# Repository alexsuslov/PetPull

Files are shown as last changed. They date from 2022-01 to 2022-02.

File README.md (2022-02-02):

# PetPull - станок для производства филамента из ПЭТ бутылок

Так что во избежание вселенского бурления - будем использовать название PetPull.
Во первых это название уже стало именем нарицательным. Первым был все же Моторист, а до него еще кто то.
Первые станки были не для для 3D печати, а для метелок...  

На основе разработок 

- Виталия Богачева

_кидайте issue если нужно что то поправить/добавить_

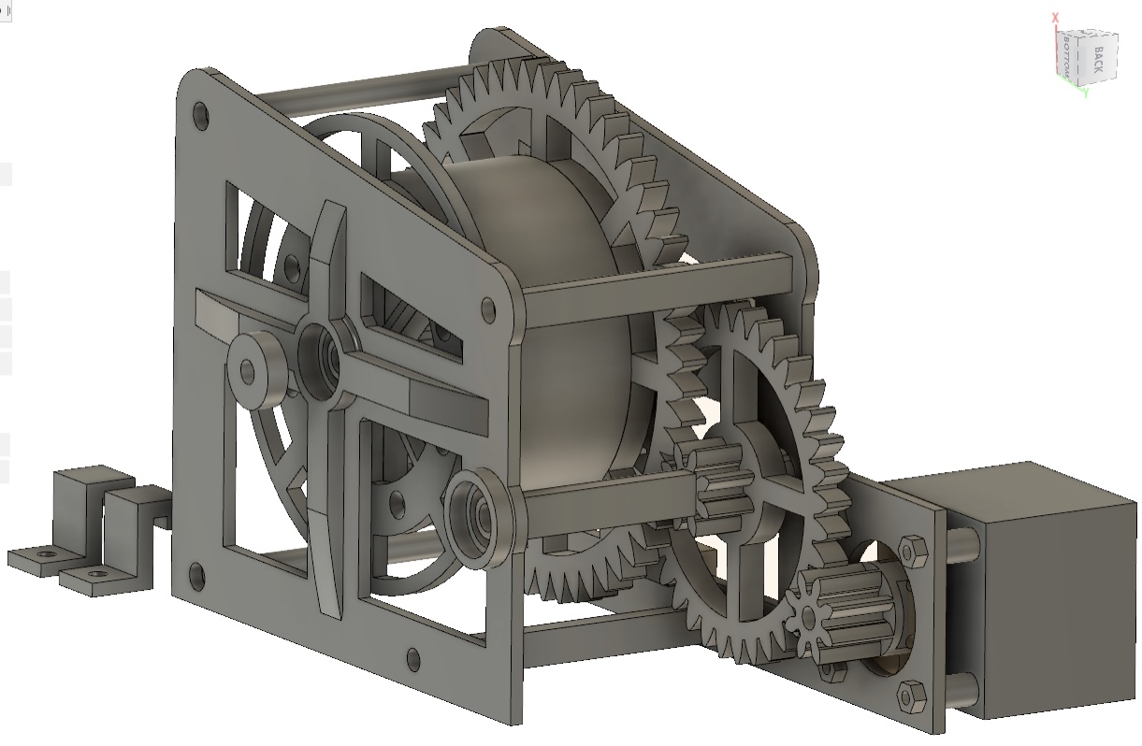
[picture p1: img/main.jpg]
main view


Простое, функциональное устройство для переработки бутылок в филамента.  

- [Обзорное видео тут](https://youtu.be/G16bqoB8Z38)
- [Схема устройства](pdf/2019-11-28V1.2.pdf)
- [Печатная плата для ЛУТ](https://drive.google.com/open?id=1dySD1lTDA4rSZQcVADHj6VBQWqIWLeg4)

## Материалы

- Двигатель - Nema 17
- Контроллер - Arduino Nano V3 
- Драйвер - A4988
- Дисплей - LCD 1602 (HD44780)
- Термистор - 100К от 3D принтера
- Нагреватель - 12V*40ВТ от 3D принтера 
- Блок нагревателя -  E3D Volcano от 3D принтера
- Сопло - 0,8мм диаметром для принтера Anet A6
- Металлический уголок из строительного магазина 
- Подшипники - 625ZZ (опционально) 16mm - 5mm

Маленькие саморезы для сборки составной детали бобины  и большие для крепления станка к основанию. 

## Характеристики 

- Энергопотребление - менее 40Вт*ч
- Скорость производства филамента ~ 10-20 см/мин
- Диаметр прутка - 1,7мм^2
- Заполнение прутка ~ 60-80%
- Рабочая температура ~ 160

## Руководство по самостоятельной сборке

- [Копус станка](assembly.md)
- [Сопло экструдера](extruder.md)
- [Бобина для намотки филамента](spool.md)
- [Контроллер скорости протяжки и температуры](controller.md)

## Температура. 
Вопреки оригинальному видео Виталия - я выяснил что температура 250-260С избыточна для производства филамента. В помещении начинает нещадно вонять, как на промзоне Парнас в Питере. При 160 градусах протяжка проходит ровно точно так же, но пластик почти ничем не пахнет.  Работоспособность станка сохраняется и при снижении температуры до 140С, но диаметр прутка начинает плавать. Видимо это не совсем подходящий режим волочения.  
[WIKI: Свойства PET(Полиэтилентерефталат) ](https://ru.wikipedia.org/wiki/%D0%9F%D0%BE%D0%BB%D0%B8%D1%8D%D1%82%D0%B8%D0%BB%D0%B5%D0%BD%D1%82%D0%B5%D1%80%D0%B5%D1%84%D1%82%D0%B0%D0%BB%D0%B0%D1%82)

## Минусы технологии

### Пруток короткий.
Прутки из бутылок получаются относительно короткими - 8-20 метров. Для печати большинства небольших деталей этого достаточно, но все же удобнее когда перед началом печати у Вас хотя бы сотня гарантированных метров пластика на катушке. 
Проблему может решить сварочный аппарат для прутков и я позже его продемонстрирую. В контроллере станка для него все предусмотрено.    
Пруток прямой и жесткий 
Норовит размотаться с катушки. Решить можно либо фиксацией свободного хода катушки, либо свиванием прутка при производстве. Пока не думал над этим. 
### Не пруток, а трубка
Думаю если сообщество подключится к вопросу - сможем обеспечить более плотное прессование ленты в прутке. Тут нужно экспериментировать. 
### Толщина ленты разнится от бутылки к бутылке
А следовательно пруток имеет разное заполнение и нужно как-то нормировать скорость подачи пластика. Пока не думал над этим. но думаю решаемо.
### Медленная скорость печати. 
Похоже особенность всего PET пластика.

## Плюсы технологии

Помимо очевидных, тертых-перетертых хочется отметить еще несколько. 

### Отсутствие страха остаться без филамента. 
Это реально круто, когда тебя не особо беспокоит сколько метров у тебя осталось в катушке. Ты знаешь, что если нужно - через пару часов будет столько сколько нужно. 
 
### Пластик более термостойкий и прочный чем ABS и PLA
Экспериментов еще не ставил, но что подсказывает мне что детали можно будет использовать в широких пределах температур и агрессивных средах. Шестерни и втулки из этого пластика реально очень прочные и износостойкие.

### Печать без головной боли
Вчера нужно было печатать ABSом. Время было дорого и нужно было поскорее завершить распечатку деталей.  Поймал себя на мысли что привыкнув печатать PETом, возвращаться к ABS, было неприятно. Это и горячий стол, и деламинация, и платно в конце концов. 

## Спайка прутка
Одно из главных неудобств при печати пластиком из бутылок - маленькая длина - всего 8-10 метров. Печатать объемные детали не удобно - нужно постоянно контролировать печать и своевременно менять материал. Задача сварки отрезков прутка - успешно решена. Расскажу как. 

### Теория
ПЭТ пластик плавится при температуре выше 260 градусов. При медленном охлаждении - кристаллизуется приобретая белый цвет,  прочность и хрупкость. При быстром охлаждении остается прозрачным и гибким. Для печати подходит второе состояние, следовательно для получения хорошего шва - нужно его быстро охладить. Требуемая скорость охлаждения около 70 градусов в секунду.  

### Блок нагрева
Для нагрева прутка я изготовил блок нагревателя из отрезка алюминиевого радиатора. В нем нужно просверлить сквозное отверстие диаметром 6мм под ТЭН, сквозное отверстие диаметром 4мм для термотрубки и глухое отверстие диаметром 2мм под датчик температуры. Последнее нужно сделать подальше от ТЭНа и поближе к термотрубке. 

После сварки нужно быстро охладить шов. Для этого подойдет алюминиевый или медный радиатор. В нем нужно сделать сквозное отверстие диаметром 4,2-4,5мм. Вдоль отверстия на поверхность делается пропил шириной 2-2,5мм для установки и извлечения прутка. 

Сварка ABS или PLA пластика не отличается от сварки PET прутка за исключением того что для нее нужна температура ниже - 160-200 градусов.

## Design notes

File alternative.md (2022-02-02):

- https://github.com/mvbasov/PETCTL
- https://t.me/s/PETPullGroup

<!-- нагреватель -->
- https://github.com/mvbasov/PETCTL/tree/github/3D_models/HeatedBlock

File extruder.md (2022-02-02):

# Экструдер

## Сопло экструдера.

В моем случае было использовано сопло изготовленное из болта с диаметром резьбовой части - 5 мм.

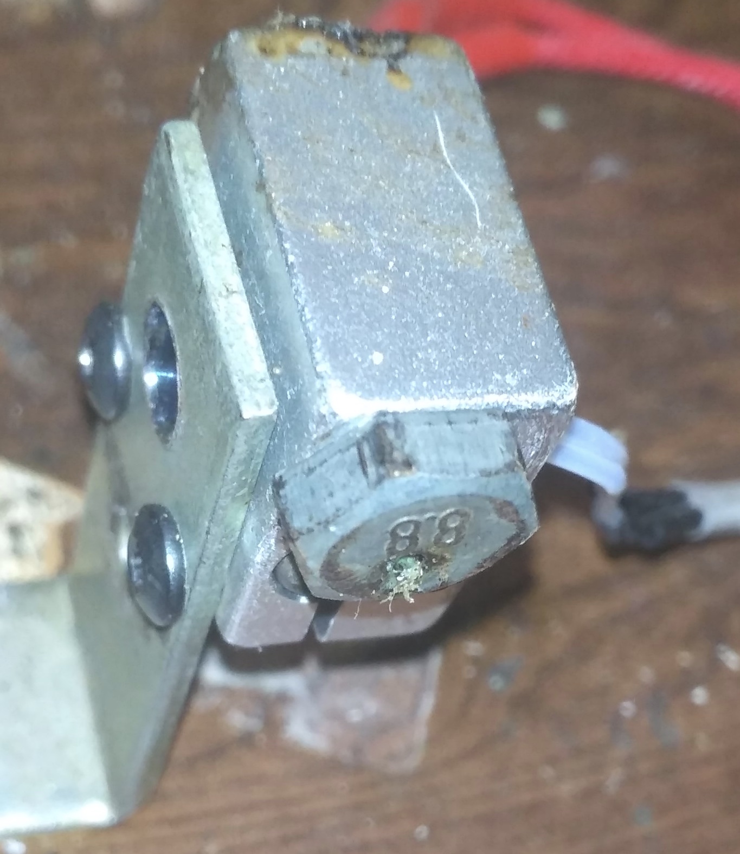
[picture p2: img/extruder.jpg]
extruder


Он был обрезан до общей длины ~10мм. Затем в центре было просверлено отверстие диаметром 2мм. Такой диаметр слишком большой для производства филамента, поэтому для его уменьшения был использован шарик от шарикоподшипника.  Несколько ударов молотка по шарику установленному на выходном отверстии экструдера - и его диаметр сужается до необходимых 1,7мм. 

У меня также был опыт использования в качестве экструдера штатных сопел устанавливаемых в принтер Anet A6. Но после нескольких неудачных попыток протяжки филамента - я отложил их до лучших времен. 
03,12,2019 - UPD 
Вполне неплохо показали себя рассверленые родные длииинные сопла для нагревателя вулкан.  
22,12,2019 - UPD

Сейчас делаю так. Беру болт М6 с длиной резьбовой части 10мм(накручиваем 2 гайки и отрезаем ножовкой). Затем подбираю сверло по фактическому диаметру 1,7мм и просверливаю болт насквозь. Затем раздаю перьевыми сверлами по кафелю. 

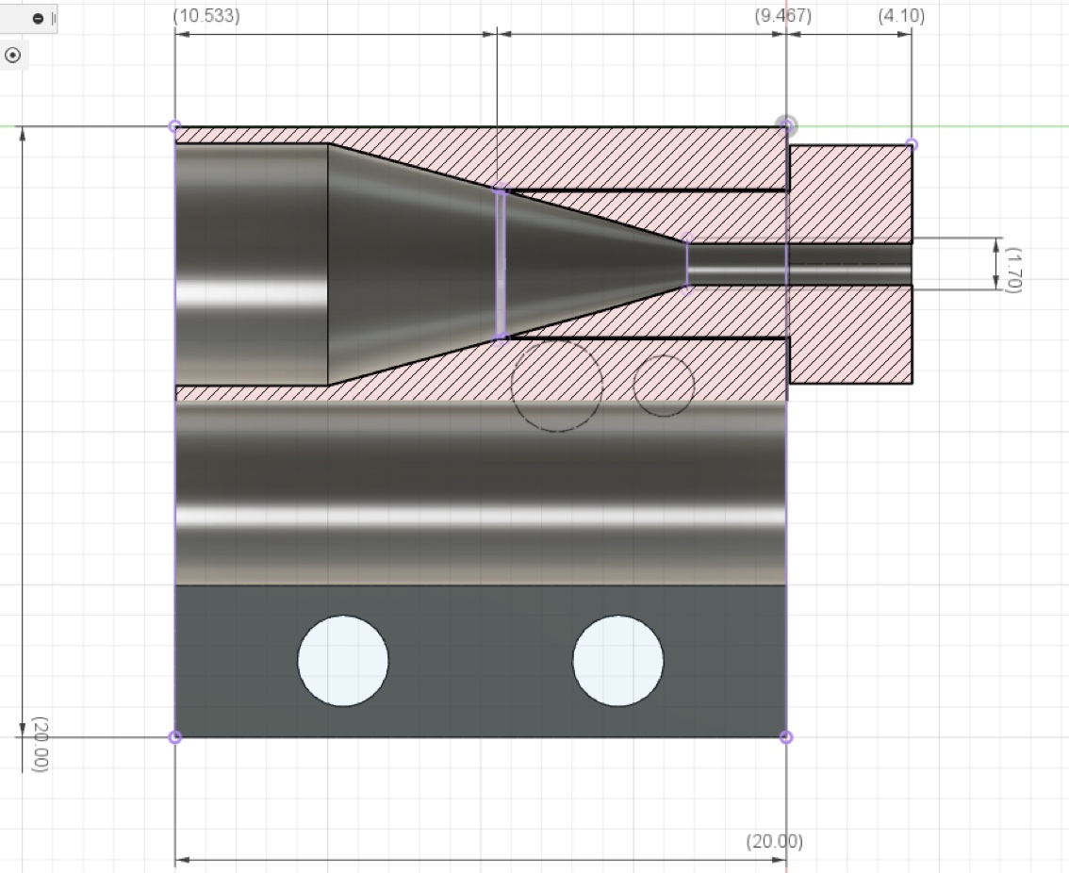
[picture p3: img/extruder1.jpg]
extruder1


## Нагреватель

Изготавливается путем высверливания конического отверстия в блоке Volcano

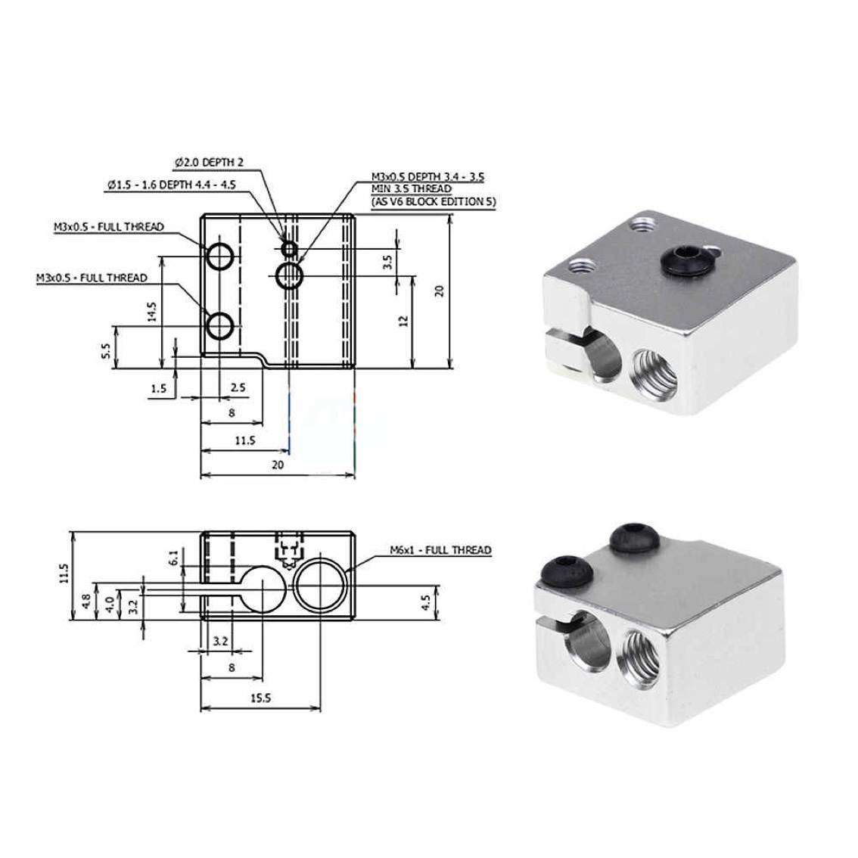
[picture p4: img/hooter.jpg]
hooter


с помощью перьевого сверла по кафелю, диаметром 8мм.

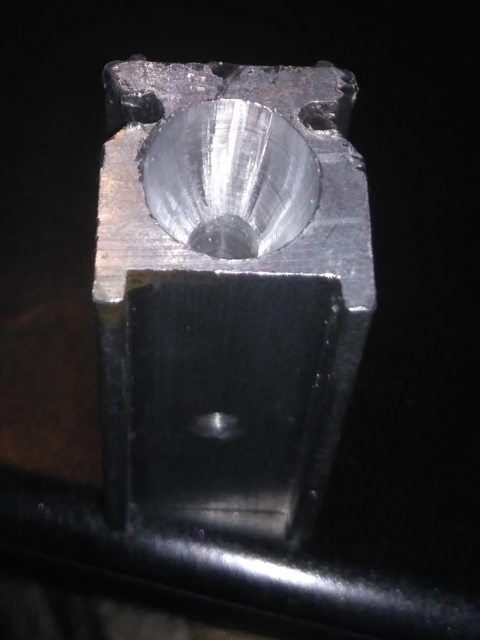
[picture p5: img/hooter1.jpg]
hooter1


Высверливание продолжается до тех пор пока кончик сверла не коснется латунной поверхности сопла. Контроль ведется визуально. 
Для крепления блока нагревателя к рабочему столу станка - используется обычный металлический строительный уголок. В нем просверливаются пару отверстий под штатные винты, зажимающие керамический ТЭН. 

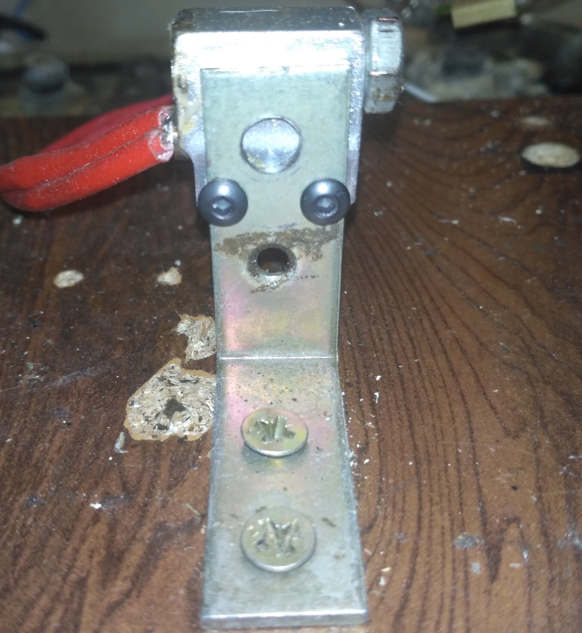
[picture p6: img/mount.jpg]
mount


Никакой теплоизоляции не используется. PID регулятор контроллера держит температуру в заданных пределах очень точно, компенсируя теплопотери. Ниже посекундный график, показывающий дрейф температуры в пределах нескольких разрядов АЦП на протяжении часа реальной работы станка. 

вот так выглядит общая работа ПИД регулятора. 

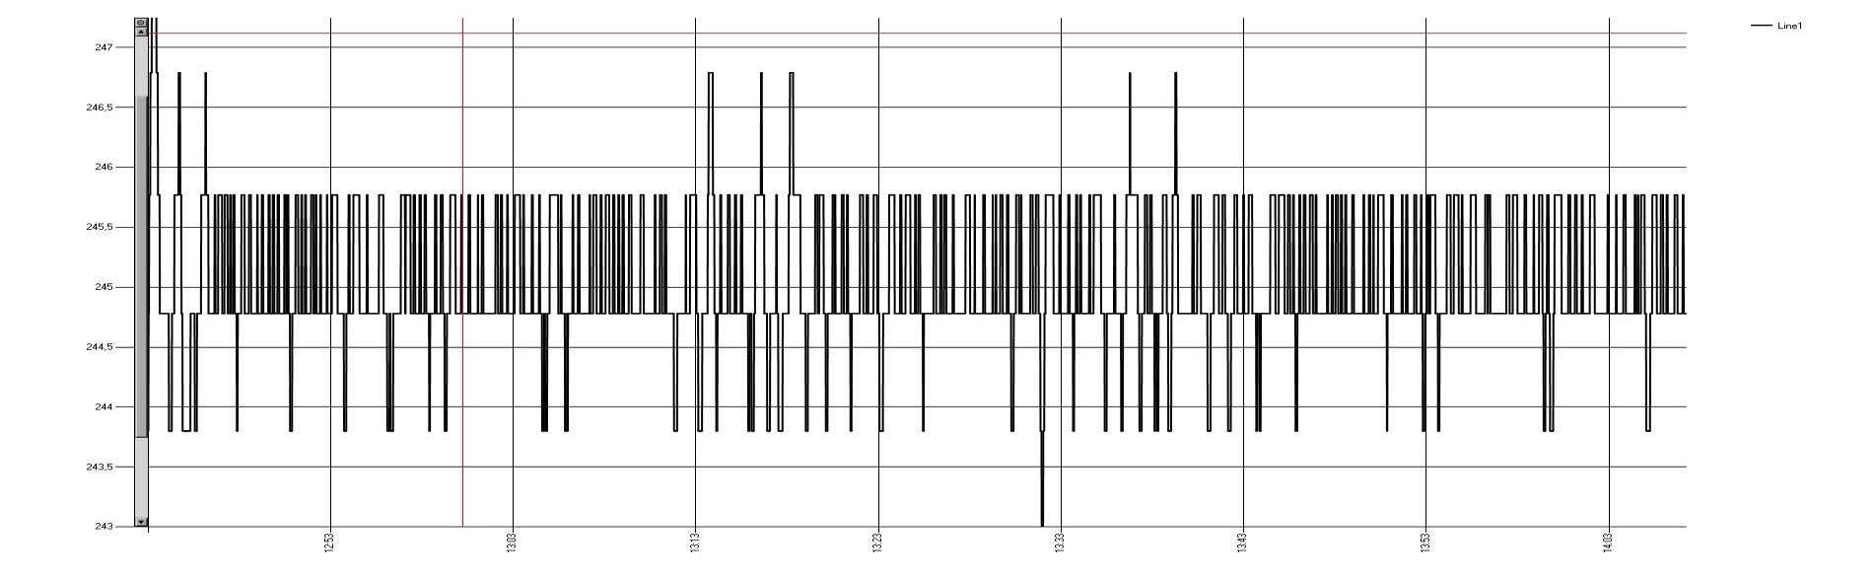
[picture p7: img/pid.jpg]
pid

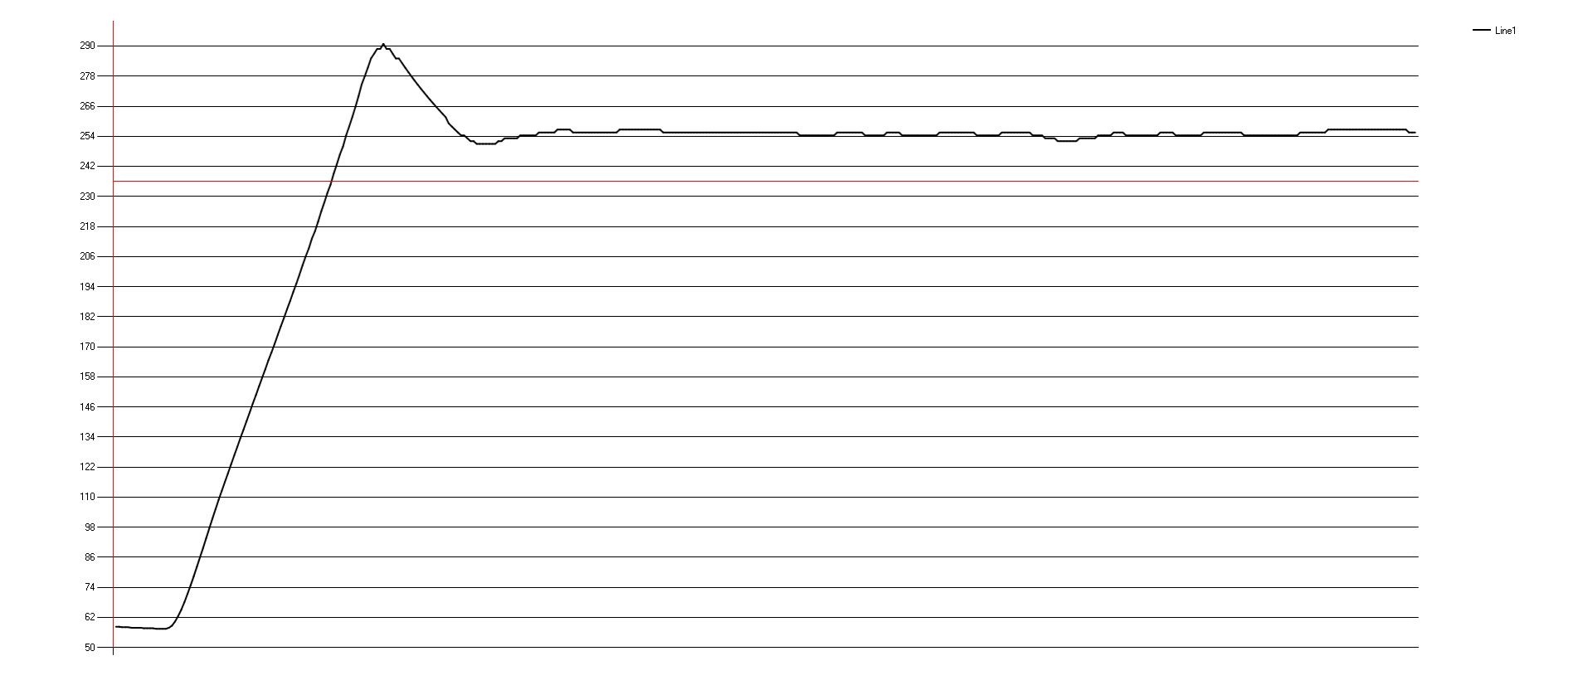
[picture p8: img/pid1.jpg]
pid1


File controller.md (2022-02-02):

# Контроллер скорости протяжки и температуры

Изготовлен на основе платки Arduino Nano V3.  Схема простейшая, не имеет дефицитных деталей, простая для повторения.  
Печатная плата выложена в репозитории. Хоть и полностью функциональная - пока не совсем готова для корпусирования. Опыта в этом у меня не много. Потому получается не с первого раза.

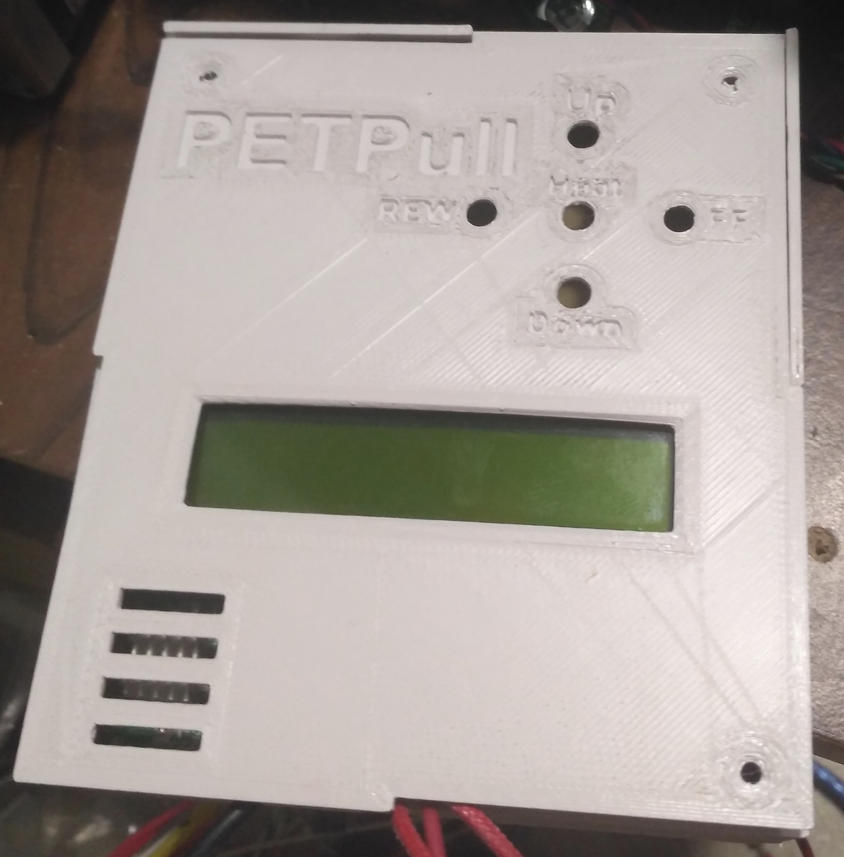
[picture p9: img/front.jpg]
front

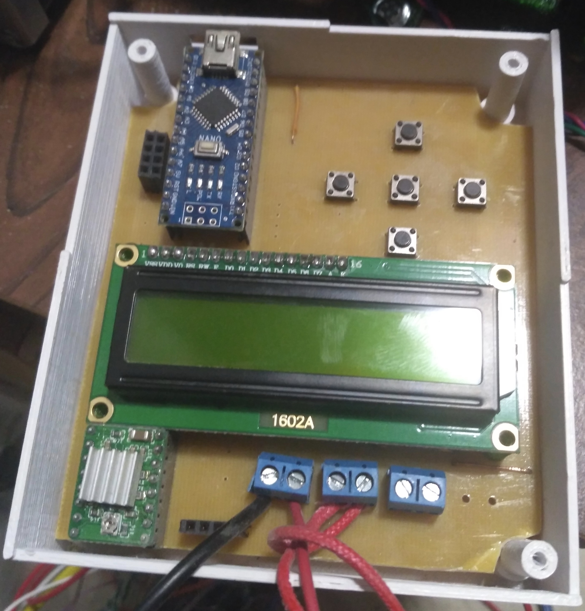
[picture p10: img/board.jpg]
board

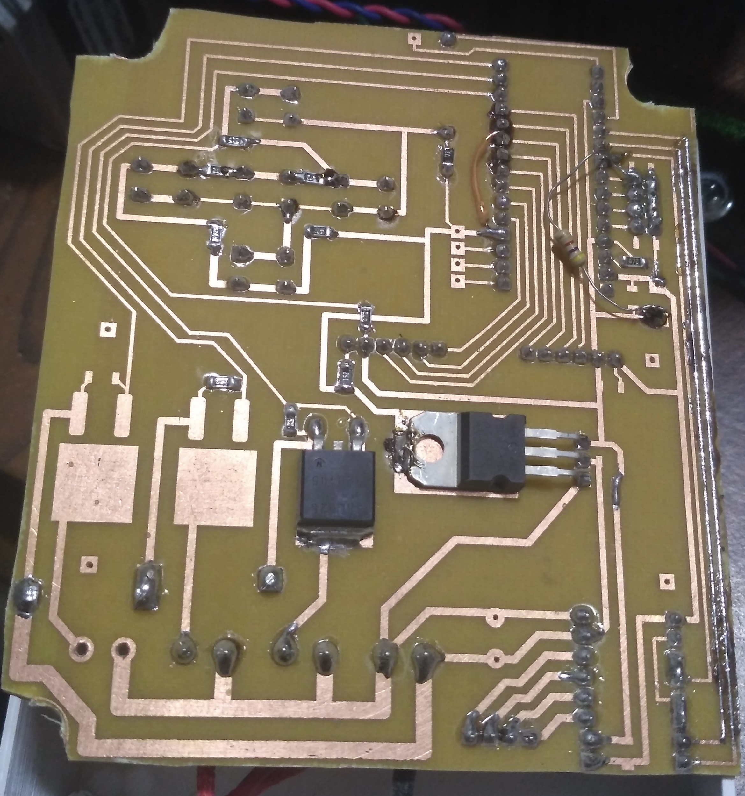
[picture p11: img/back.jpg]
back


Установки температуры и скорости протяжки запоминаются. Планируется дописать подсчет произведенных метров филамента. Оптимизировать режимы протяжки. 
Работа контроллера очень стабильна. При сборке я специально не использовал фильтрующие конденсаторы по питанию. Несмотря на это плата управления ни разу не сбоила. Если даже в таком режиме ничего не идет в разнос, то после установки емкостей по питанию - все будет совсем железобетонно. 
В рабочем режиме звука двигателя почти не слышно. 

## Прошивка 
Прошивка как всегда простейшая. Включает в себя три шага. 
1) Скачивание последней прошивки из репозитория: 

- https://drive.google.com/open?id=1S7iesOyFmSDcyv66gEf9Ux55c0caf5wk
- [Скачивание программы которая умеет прошивать ардуино бинарными файлами](https://drive.google.com/open?id=1HEsLZSfcgszGMGvXLtFU6XibcUySJIrJ)
- [Описание программы](http://www.getchip.net/posts/136-gc-uploader-avtomaticheskijj-zagruzchik-hex-fajjlov-dlya-arduino/)

2) Подготовка EEPROM микроконтроллера. 
Желательная процедура для гарантированной очистки содержимого энергонезависимой памяти и исключения возможных ошибок при дальнейшем обновлении прошивки. В большинстве случаев не требуется, но настоятельно рекомендуется. Дело в том что в ПЗУ процессора могут остаться старые данные с которыми станок будет работать не корректно. Для того чтобы их удалить загрузите в ардуину скетч. 

```
#include <EEPROM.h>
void setup() { for (int i = 0 ; i < 512 ; i++) {EEPROM.write(i, 255);}}
void loop() {}
```
После того как прошили им ардуино - подождите 10 секунд и прошивайте основное ПО.

3) Прошивка основного ПО 
Запускаем программу gcUploader для заливки бинарных файлов.HEX в Ардуино.

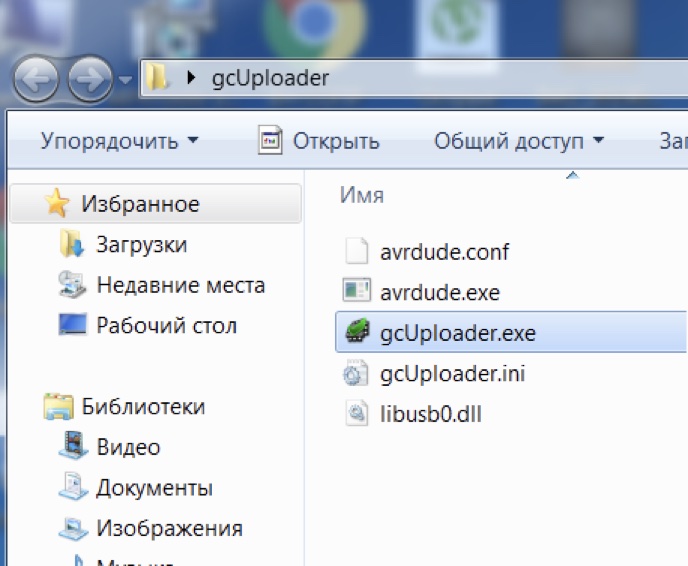
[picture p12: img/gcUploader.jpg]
gcUploader


Подключаем ардуино к компьютеру.  
- Кликаем шестеренку в запустившемся окне программы. 
- Если Вы меняли загрузчик на UNO указываем тип платы - UNO!!!
- Если у Вас новая плата указываем тип платы - NANO!!!
- Проверяем правильность порта подключения Ардуино(если не тот - меняем на актуальный). 
- Перетаскиваем скачанный файл основной прошивки на окно программы. 
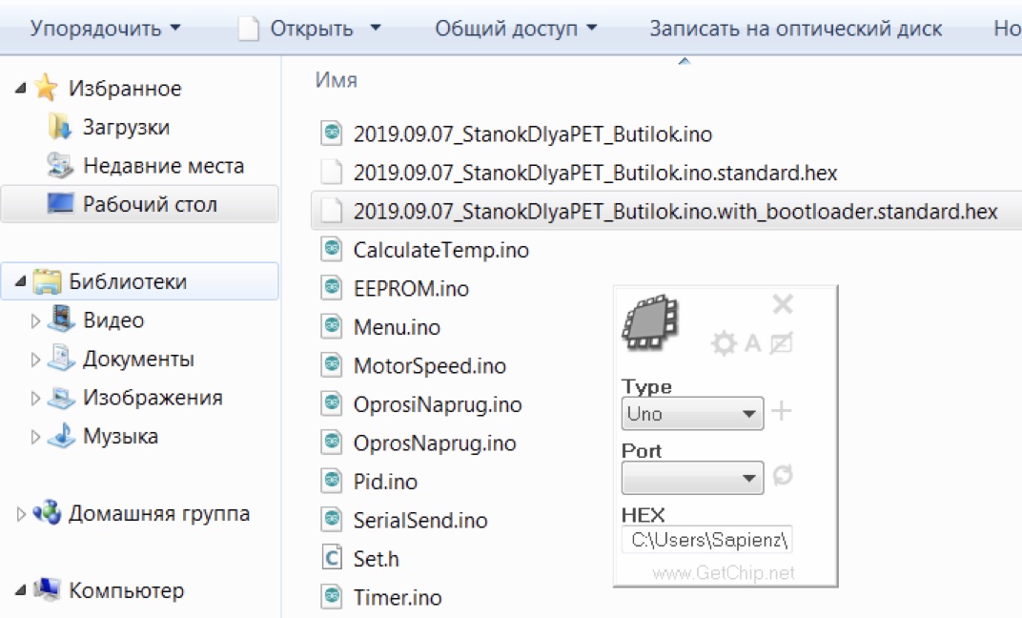
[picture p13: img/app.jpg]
app


И нажимаем пиктограмку с двенадцатиногой микросхемой для старта заливки ПО.
Все! Можно пользоваться! 

Рассматриваются варианты рассылки готовых силовых плат, после доводки до финального состояния.

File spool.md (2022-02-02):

## Бобина для намотки филамента

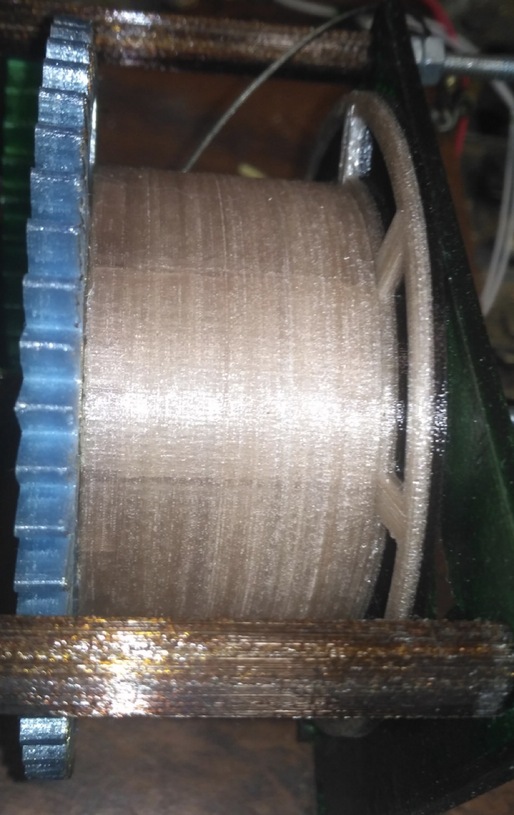
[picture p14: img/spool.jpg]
spool


Эта деталь состоит из трех составных частей.  
Шестерня - передает крутящий момент на тело бобины. 
Ее зубья испытывают максимальные усилия при протяжке прутка. 
Ее желательно изготавливать из износостойкого пластика типа PET, PETG или нейлона. 
В результате протяжки сотни метров прутка одна (рабочая) плоскость зубьев шестерни из ABS примялась, 
но можно с уверенностью сказать, что полкилометра - километр она протянула бы. 
Шестерня из PET при том же пробеге не имеет видимых деформаций. 
Тело бобины - деталь на которую наматывается пруток. Общая нагрузка - средняя. 
Можно печатать из любого типа пластика. 
Крышка бобины - деталь испытывающая нагрузки только когда к ней подходит навиваемый пруток. 
Очередной виток пытается втиснуться между предыдущим и крышкой бобины. Тем самым пытается оторвать крышку от тела бобины. 
Этому должны помешать восемь маленьких саморезов которыми крепится крышка к телу бобины. 
В первом прототипе было всего два самореза и их вырвало без особого труда.  
С восемью саморезами проблем не возникало. Печатать крышку можно любым типом пластика.

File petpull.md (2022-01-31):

# Меню контроллера (версия 2.3)

На единой плате объединены два независимых устройства - станок по вытяжке прутка из бутылок и спайщик отрезков производимого прутка. Меню контроллера также поделено на два направления. При движении по пунктам меню вверх - управляем настройками спайщика.  При движении по пунктам меню вниз - управляем настройкой вытяжки прутка. 
Для перемещения по пунктам меню используются кнопки вверх и вниз.
Для изменения режимов используются кнопки влево и вправо. 
В нескольких пунктах меню также задействована средняя кнопка. Она позволяет выбрать дополнительные настройки. 
При первоначальном запуске контроллер несколько секунд отображает версию прошивки.
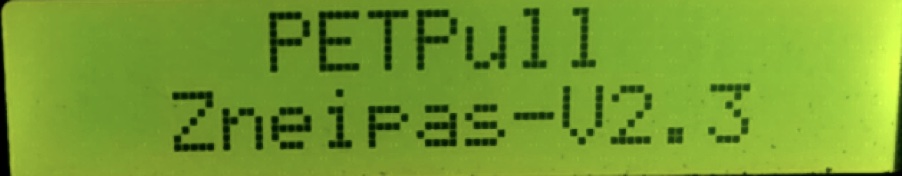
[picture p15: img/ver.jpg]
ver

Затем по умолчанию отображается режим вытяжки прутка.

## Режим вытяжки прутка (стартовое меню).
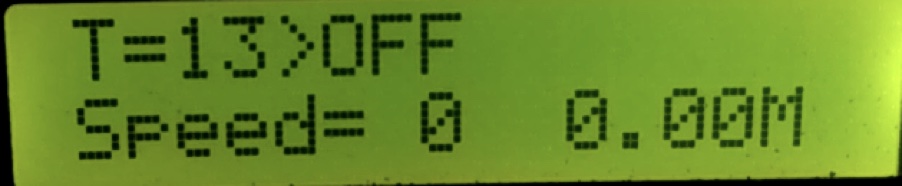
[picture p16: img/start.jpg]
start

```
T=13 > OFF
```
текущая температура нагревателя вытяжки прутка(13 градусов). Нагрев выключен(OFF). Для того чтобы включить нагрев - нужно однократно нажать среднюю кнопку клавиатуры. Первая строка сменится на примерно такую:
```
T=13 >200>200C *
```
- где текущая температура(13 градусов) стремится(>) к стартовой (200 градусов), а после некоторой работы станка 

на стартовой температуре, нагрев установится (>) в рабочую температуру(в данном случае тоже 200 градусов).  Чем отличаются данные температуры - покажу чуть позже.

## Настройка скорости вытяжки прутка. 
На второй строчке экрана можно видеть текущую скорость протяжки. При нажатии  вправо - станок начнет вытяжку прутка на первой скорости. 
```
SPEED= 1
```
При повторном нажатии кнопки вправо - станок увеличит скорость протяжки вдвое.
```
SPEED= 2
```
При следующем нажатии - втрое.
```
SPEED= 3
```
То есть базовая скорость - первая, повторные нажатия просто кратно увеличивают ее.  
Если еще раз нажать кнопку вправо -  станок переключится в режим перемотки готового прутка и увеличит скорость движения бобины ~ в 20 раз.
```
SPEED= 4
```
Данный режим нужен именно для смотки с бобины уже готового прутка. 

Кнопка влево переключает скорости взад, заставляя бобину сначала замедляться а потом начинать движение в обратную сторону.  

И базовая скорость протяжки и скорость смотки регулируются в настройках. Чуть позже рассмотрим процесс регулировки. 

## Подсчет метража вытянутого прутка. 
```
0.01M
```
Станок при движении на скоростях с 1 по 3ю подсчитывает приблизительный метраж производимого прутка. При движении на скоростях от -4 до 0 - подсчет метров не производится. Следует учитывать что поправки на диаметр намотки нет и фактическая длина прутка будет несколько больше отображаемой. Это не так страшно как может показаться на первый взгляд. Печатаем мы уже спаянными отрезками филамента и требуемый объем пластика определяется на глазок.

Для того чтобы обнулить счетчик метров между протяжками нужно дважды нажать на среднюю кнопку клавиатуры. При этом выключится и снова включится нагрев. Одновременно счетчик метража обнулится.

```
*
```
- индикация работы ПИД регулятора нагревателя вытяжки. 

В правом верхнем углу экрана можно видеть символ звездочки.  По нему визуально можно контролировать работу ПИД регулятора протяжки. В момент подачи напряжения на нагреватель - звездочка загорается. В момент отключения нагрева - гаснет. Функция из разряда удобств. Полезности особой не несет.  

## Меню настройки температуры вытяжки ленты.

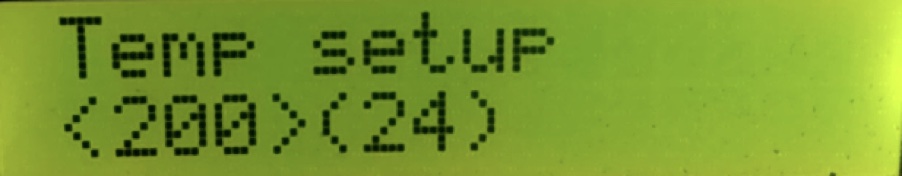
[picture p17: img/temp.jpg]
temp


Данное меню  позволяет настроить температуру вытяжки прутка.  Расположено сразу после стартового, при нажатии кнопки вниз, для быстрой настройки в процессе работы. 
Кнопками влево/вправо можно задавать температуру переработки. Она может принимать значения в диапазоне от 1 до 320 градусов. В скобках показывается текущая температура. 
По умолчанию  выставлена температура 180 градусов. Она не дает сильного запаха при переработке, источником которого выступает как сам пластик, так и остатки клея на разрезаемых бутылках. Сейчас все чаще использую температуру в 200 градусов. Станку проще тянуть ленту и шаговик не срывается.  

## Меню настройки стартовой температуры.

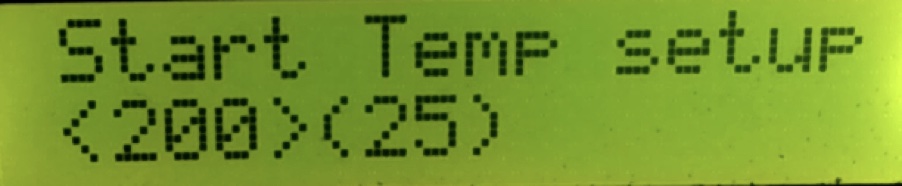
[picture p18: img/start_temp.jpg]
start_temp


Лента проще сворачивается в пруток при большей температуре, тянуть ее можно при этом с меньшим усилием. Для того чтобы дать возможность станку сделать хотя бы один виток прутка на бобину с меньшей нагрузкой было дополнено меню стартовой температуры.  Данная температура регулируется кнопками влево/вправо. В скобках отображается текущая. Будет действовать при старте станка на первых 25 сантиметрах прутка. После этого контроллер переключится на удержание температуры установленной в Меню 2. Стартовая и целевая температуры независимы друг от друга и могут принимать значения в диапазоне от 1 до 320 градусов. 

## Меню настройки скорости вытяжки прутка. 
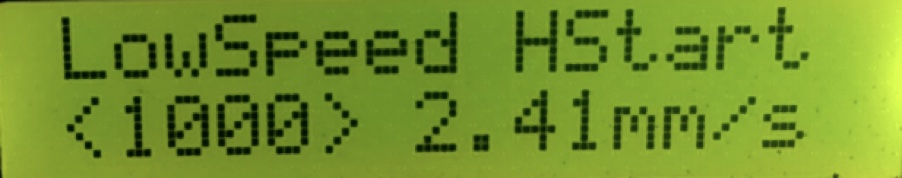
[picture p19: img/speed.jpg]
speed


Меню скорости, с которой будет вытягиваться пруток.  По умолчанию выставлена 1000 тактовых импульсов в секунду, что соответствует скорости 2,41 мм/сек.  Изменять ее можно кнопками влево/вправо при этом отображаемая скорость протяжки прутка также будет меняться. 
В прошивке реализованы два типа работы шагового двигателя:

**SoftStart** - режим плавного разгона и торможения.

**HardStart** - режим моментального разгона и торможения.

Переключиться между ними можно нажатием средней кнопки клавиатуры. 
Лично мне привычнее и удобнее режим HardStart. Он чётче определяется на слух. Но может кому - то удобнее будет плавное управление скоростью.

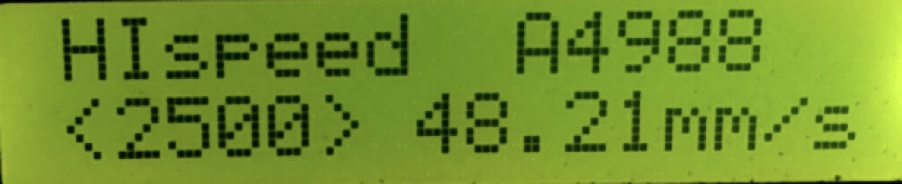
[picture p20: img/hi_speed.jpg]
hi_speed


Когда процесс переработки завершен - нужно смотать готовый пруток с катушки. Скорость с которой это делается регулируется в данном меню кнопками влево/вправо. 

По умолчанию она выставлена в 2500 тактовых импульсов в секунду, что соответствует скорости в 48,2мм/сек. 

Помимо скорости перемотки готового прутка по нажатию средней кнопки клавиатуры можно выбрать типу установленного драйвера: A4988 или DRV8825. Контроллер гарантированно поддерживает работу именно с такими драйверами. Работа с другими не тестировалась, хотя наверняка и возможна. 

## Меню выбора режима принудительного выключения.
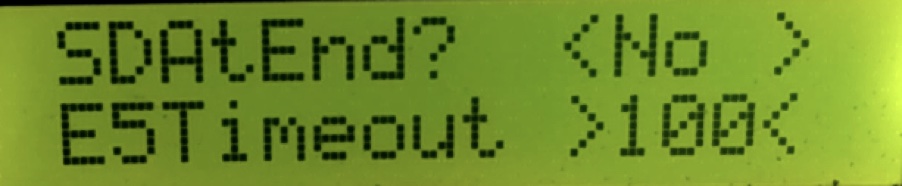
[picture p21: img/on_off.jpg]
on_off


Я уже показывал в одном из [видео](https://youtu.be/XyGHh3iFTdM)  как можно реализовать физическое отключение станка от питающего напряжения.  Кнопками влево/вправо можно активировать данный режим или отключить его. По умолчанию станок не дает сигнала на отключение питания после переработки. 
По нажатию средней кнопки клавиатуры можно выбрать таймаут ошибки E5. Данная ошибка - защитная функция станка. Для нагревателя типа Вулкан таймаут равен примерно 100 секундам.  Для более массивных нагревателей можно выбрать 200 или 300 секунд. Желательно выбирать таймаут чем меньше, тем лучше. По умолчанию стоит 100 секунд. 

## Меню настройки пропорционального коэффициента PID регулятора. 

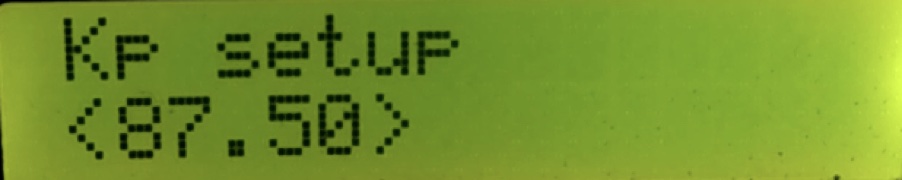
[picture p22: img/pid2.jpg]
pid


Если кому-то надо вручную выставить пропорциональный коэффициент PID регулятора - это можно сделать в данном меню кнопками влево/вправо.

## Меню настройки интегрального коэффициента PID регулятора. 
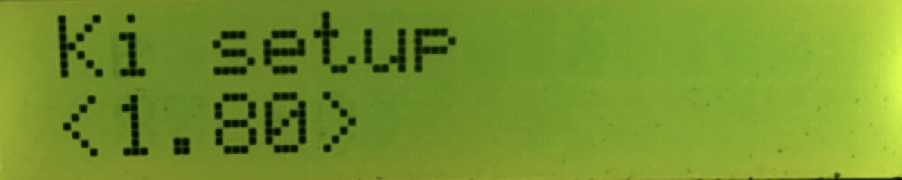
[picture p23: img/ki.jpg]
ki


Если кому-то надо вручную выставить интегральный коэффициент PID регулятора - это можно сделать в данном меню кнопками влево/вправо.

## Меню настройки дифференциального коэффициента PID регулятора
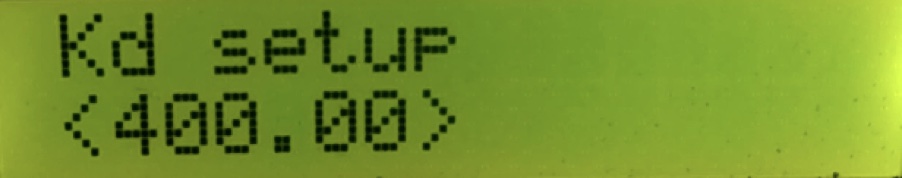
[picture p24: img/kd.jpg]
kd

Если кому-то надо вручную выставить дифференциальный коэффициент PID регулятора - это можно сделать в данном меню кнопками влево/вправо.

## Меню автоматического подбора коэффициентов PID регулятора. 
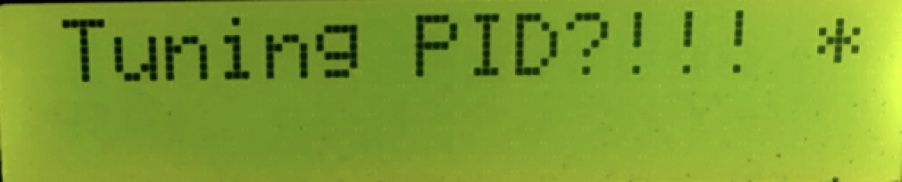
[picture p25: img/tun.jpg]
tun


Прошивка контроллера умеет находить коэффициенты для PID автоматически.  Для каждого станка, нагревателя, питающего напряжения, температуры протяжки они будут разными. 

Производить автоматический подбор коэффициентов надо сразу после включения станка,  при фактической температуре нагревателя вытяжки не выше 50 градусов. Калибровка привязывается к температуре вытяжки. То есть, если Вы планируете тянуть на температуре 200 градусов, то в меню 2 настраиваете это. Затем запускаете калибровку. Калибровка длится от получаса до полутора часов в зависимости от конструкции нагревателя, напряжения БП, целевой температуры и окружающей среды. По завершению калибровки на экране появится надпись DONE. После этого желательно выключить и включить станок снова. 

Калибровку нельзя прерывать. Если такое все же произошло - дождитесь пока нагреватель остынет и повторите ее снова. 

## Меню настройки контрастности LCD дисплея.  
contrast

Из-за того, что все LCD дисплеи разные - при первом старте станка может случиться такая ситуация, когда на экране не будет ничего видно. Для того чтобы увидеть изображение, можно вслепую (нажав 20 раз кнопку вниз), спуститься до меню регулировки контраста. Затем кнопками влево/вправо  выставить желаемый уровень контраста. Зажмите кнопку влево и не отпускайте ее не менее  минуты.  Изображение проявится. В последней версии контроллера я постарался сделать так чтобы данная ситуация не коснулась пользователей, но если все же произошло - меню контраста ВСЕГДА будет последним внизу. Вы ВСЕГДА сможете добраться до него вслепую. 
В этом же меню можно выбрать тип механики станка :
Классический PETPull (по умолчанию) или более мощную модификацию от RobertSa. 
Переключиться между ними можно при помощи средней кнопки клавиатуры. После выбора - поднимитесь до меню 4 и отрегулируйте скорость вытяжки (по умолчанию 2,4мм/сек).

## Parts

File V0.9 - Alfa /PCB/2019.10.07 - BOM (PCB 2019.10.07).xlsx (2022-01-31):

№ детали | Номинал | Корпус
R1 | 47k | 1206
R2 | 4.7k | 1206
R3 | 4.7k | 1206
R4 | 4.7k | 1206
R5 | 4.7k | 1206
R6 | 4.7k | 1206
R7 | 4.7k | 1206
R8 | 4.7k | 1206
R9 | 4.7k | 1206
R10 | 4.7k | 1206
R11 | 4.7k | 1206
R12 (необяз) | 4.7k | 1206
R13 | 4.7k | 1206
R14 | 4.7k | 1206
R15 | 1.5k | 1206
R16 | 0 ом | 1206
C23 | 1n | 1206
С1 | 100n | 1206
C2 | 100n | 1206
C2 | 100n | 1206
C2 | 100n | 1206
C2 | 100n | 1206
C4 | 100n | 1206
C3 | 220u*16V
С5 | 470u*35v
LM7805 | 1шт | TO220
Arduino nanoV3 | 1шт
LCD 1602 | 1шт
Кнопки тактовые | 5шт | 6x6x4,3 мм
Клемники | 4 шт
Драйвер A4988 | 1 шт
Logic N-MosFet 25 - 60 V (<20mOhm) -IRLR2905 | 3 шт | DPAK
Гребенки папа/мама
D1 | SMB5819 | 1206
D2 | SMB5819 | 1206
D3 | SMB5819 | 1206

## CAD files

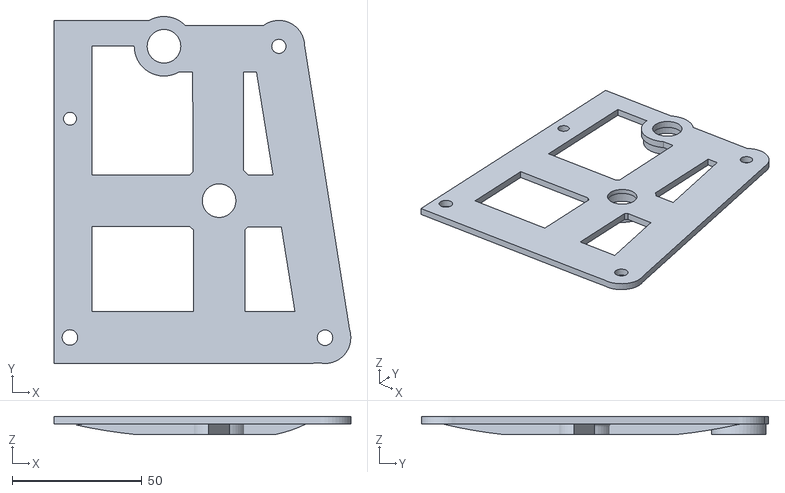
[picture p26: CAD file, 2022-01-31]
V0.9 - Alfa /3D/STL/01-02 Стенка маленькая.stl
114.6 x 134.0 x 7.00

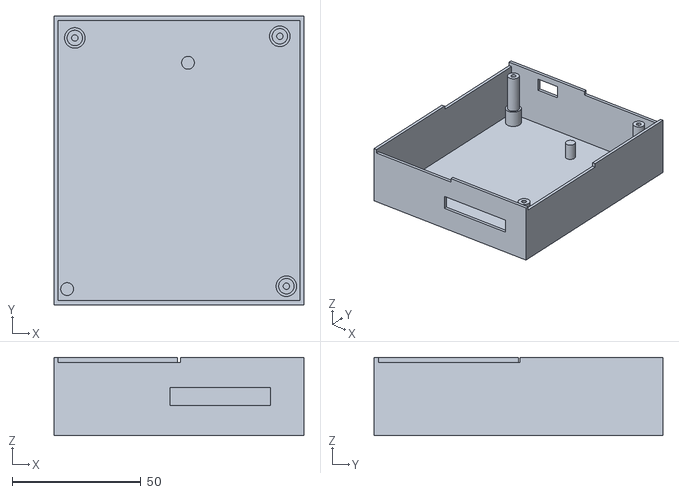
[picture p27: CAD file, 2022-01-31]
V0.9 - Alfa /3D/Корпус под самодельную плату/Коробочка.stl
97.2 x 112.2 x 30.4

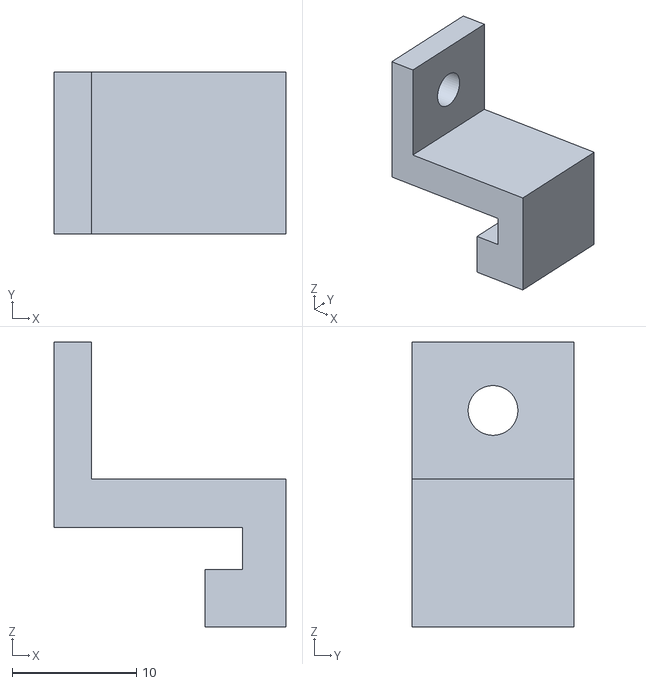
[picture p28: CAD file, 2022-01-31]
V1.0 - Release/3D модели редуктора/STL/01-03 Клипса-нужно 4шт.stl
18.6 x 13.0 x 22.9

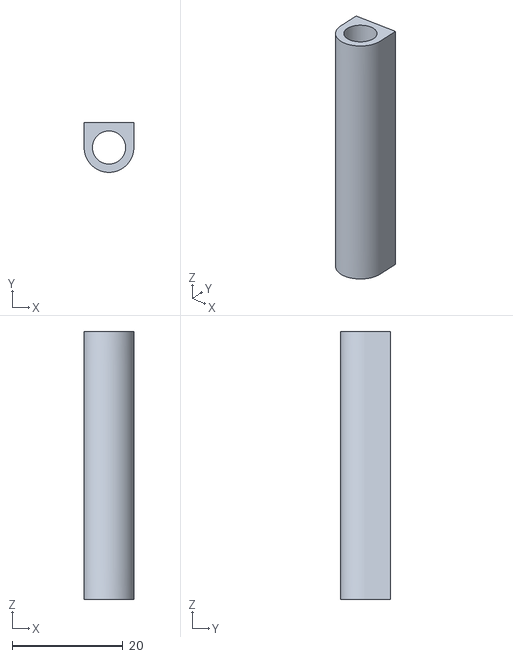
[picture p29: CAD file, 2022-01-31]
V1.0 - Release/3D модели редуктора/STL1.1/07 - Спейсер средней шестерни.stl
9.00 x 9.00 x 48.5

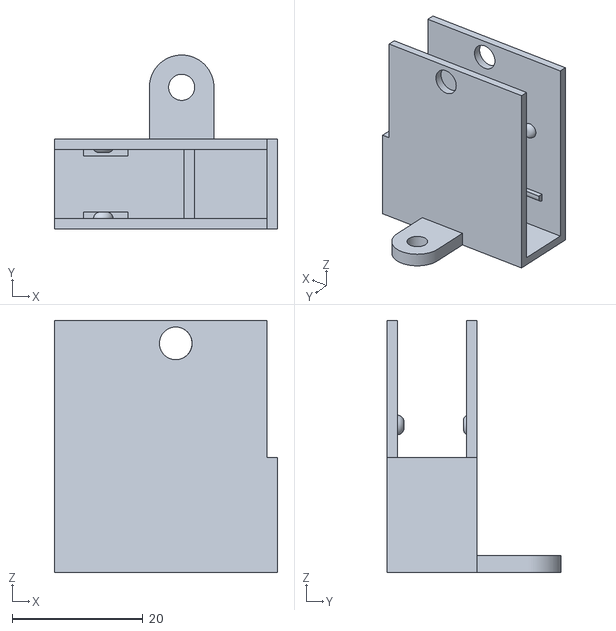
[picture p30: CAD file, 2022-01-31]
V1.0 - Release/3D модель датчика автостопа /Korpus.stl
34.2 x 26.6 x 38.6

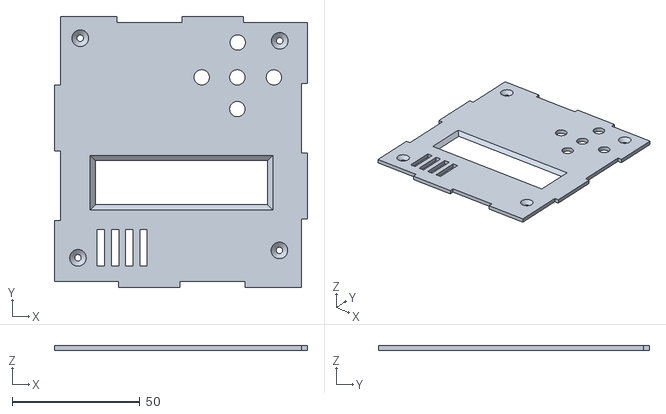
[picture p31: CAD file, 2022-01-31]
V1.0 - Release/3D модель корпуса(заводская плата)/02 - Крышка.stl
99.0 x 106.0 x 2.00

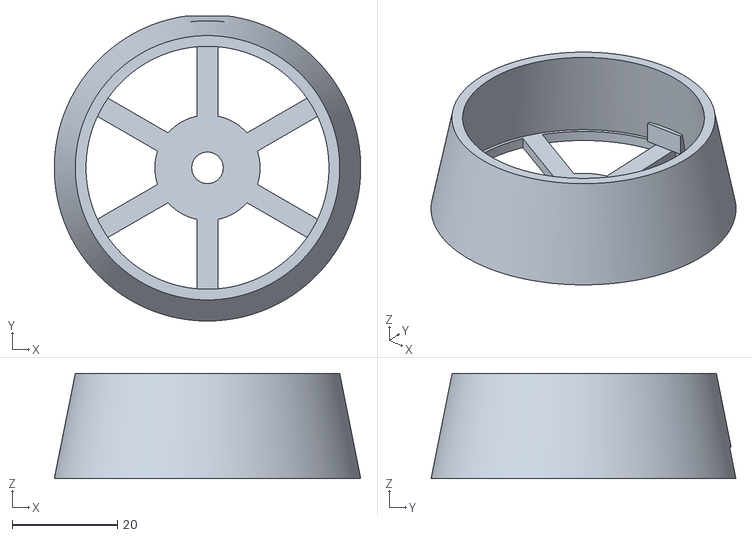
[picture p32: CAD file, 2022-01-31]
Приспособы/Катушка для временного хранения прутка /V1 (под шпильку М6)/02 - Верхний прижим.stl
58.2 x 57.9 x 20.0

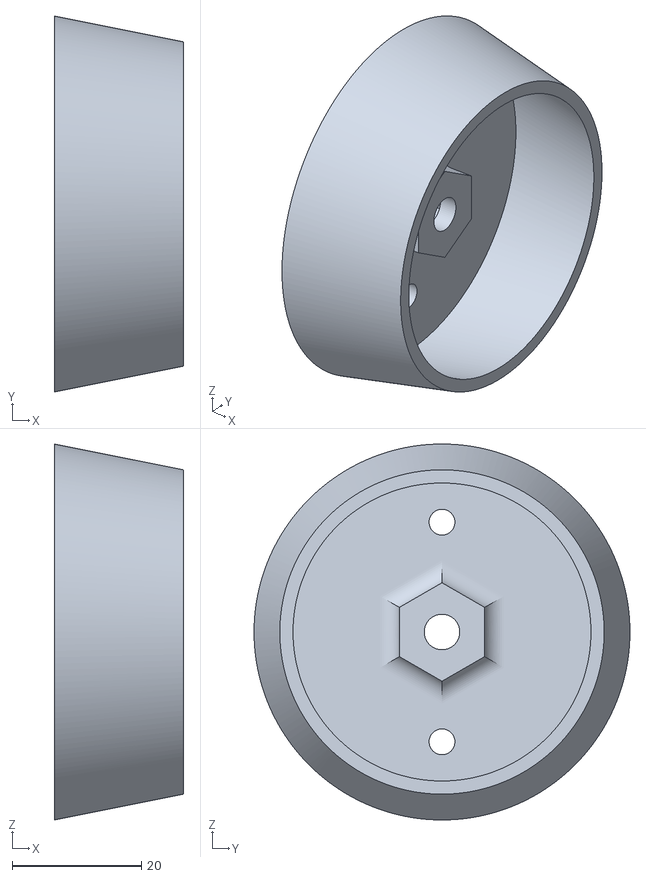
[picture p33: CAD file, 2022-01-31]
Приспособы/Катушка для временного хранения прутка /V2 (под шпильку М5)/Основание.stl
20.0 x 58.2 x 58.2

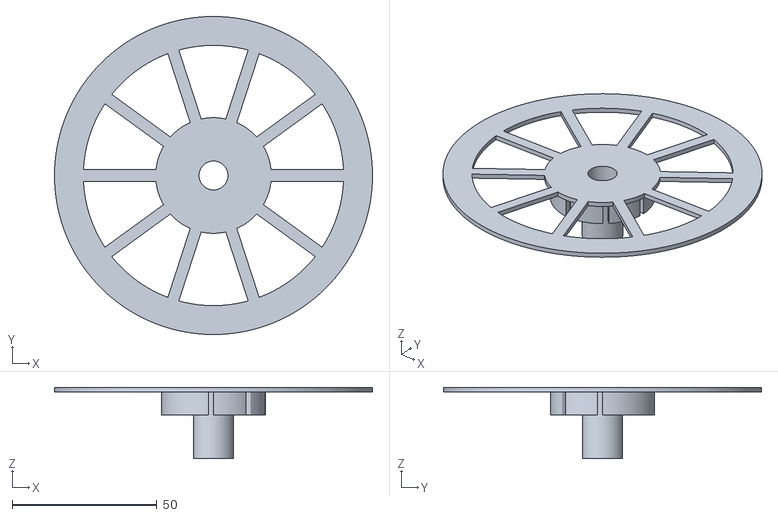
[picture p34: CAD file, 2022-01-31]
Приспособы/Катушка для ленты /01 - Шпуля.stl
110.0 x 110.0 x 24.6

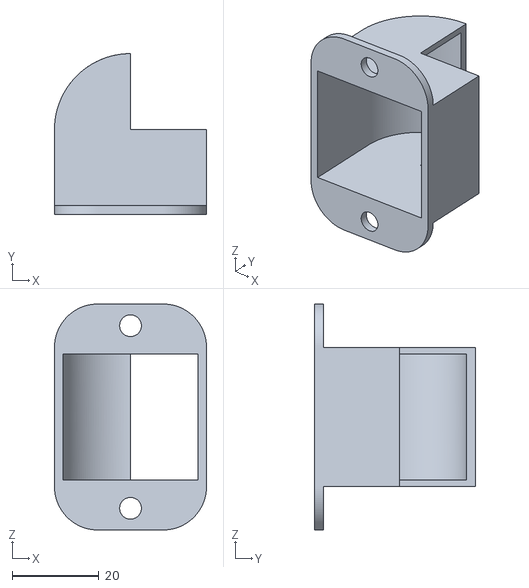
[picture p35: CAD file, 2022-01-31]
Приспособы/Корпус холодильника из бобышки 32 на 28 от кулера ПК/Корпус холодильника(27,5 на 32).stl
35.0 x 37.0 x 52.0

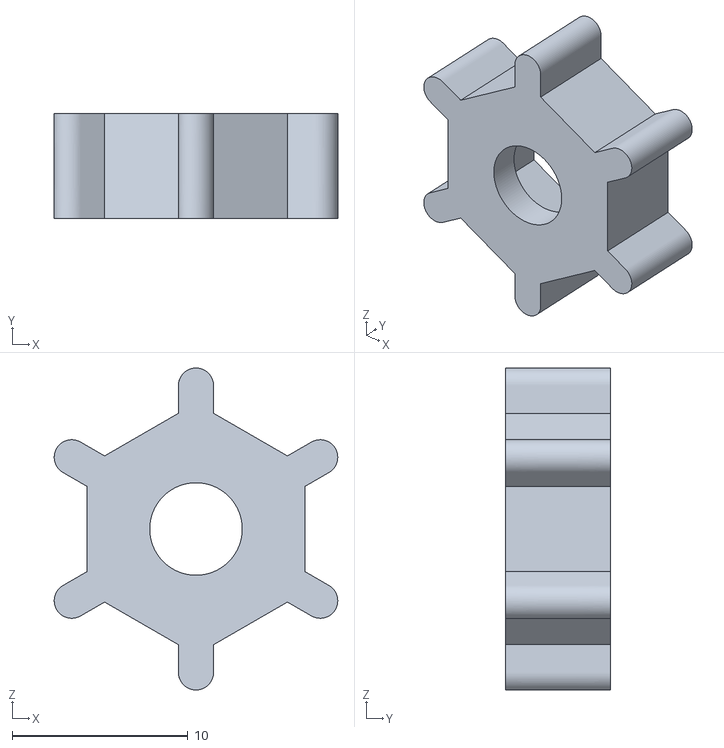
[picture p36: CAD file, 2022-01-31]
Приспособы/Наждак /04 - Барашек держателя мотора.stl
16.1 x 6.00 x 18.3

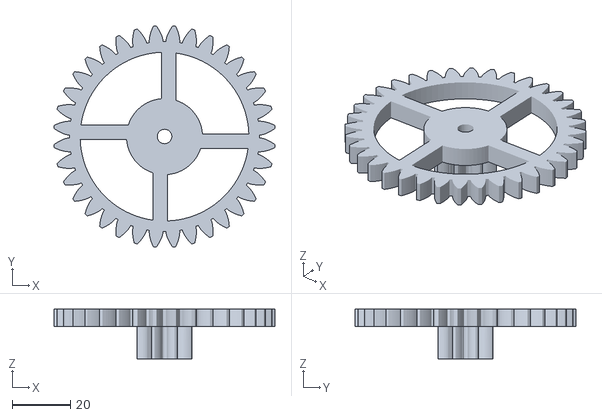
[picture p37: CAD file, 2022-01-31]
V0.9 - Alfa /3D/STL/02-01 Среднея шестерня.stl
75.8 x 75.8 x 17.1

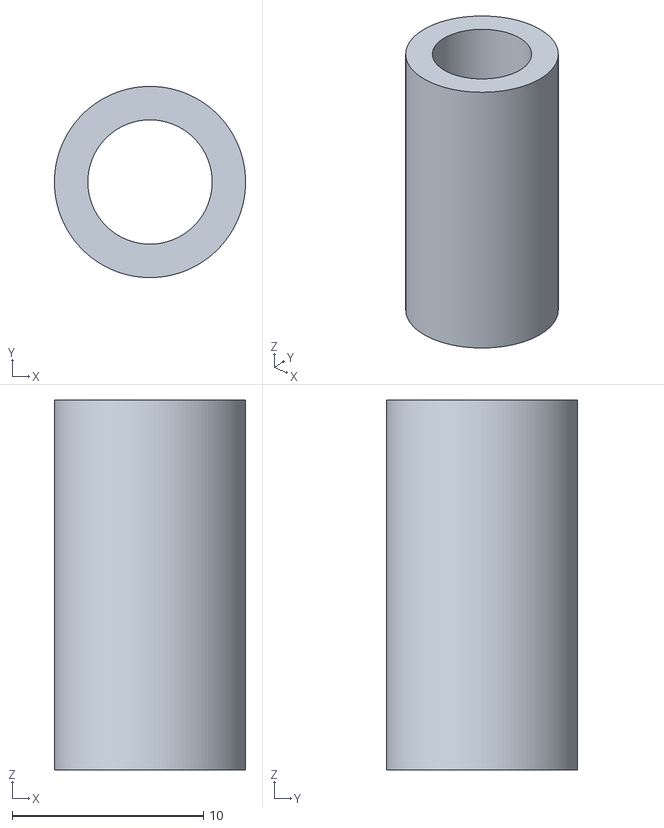
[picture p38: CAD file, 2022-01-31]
V0.9 - Alfa /3D/Корпус под самодельную плату/Проставки.stl
10.0 x 10.0 x 19.4

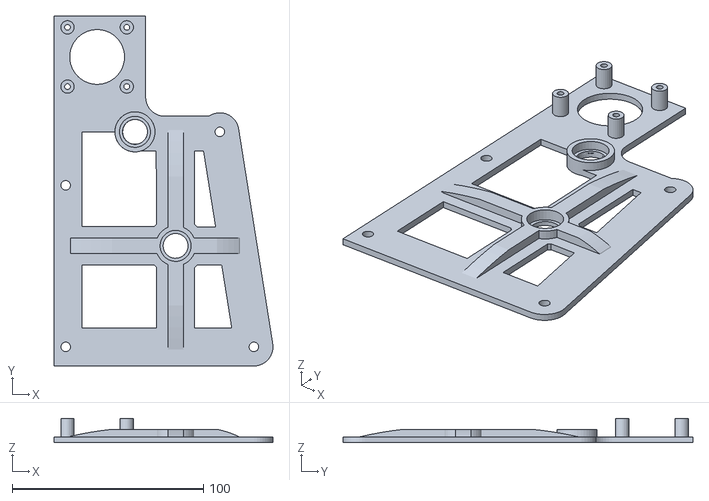
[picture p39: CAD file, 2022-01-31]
V1.0 - Release/3D модели редуктора/STL/01-01 Стенка большая.stl
114.6 x 183.1 x 12.8

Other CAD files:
V1.0 - Release/3D модели редуктора/STL1.1/14 - Шестерня малая.stl
V1.0 - Release/3D модель датчика автостопа /Kluvik.stl
V1.0 - Release/3D модель корпуса(заводская плата)/04 - Рамка дисплея.stl
Приспособы/Катушка для временного хранения прутка /V1 (под шпильку М6)/05 - Тело бобины катушки хранения.stl
V0.9 - Alfa /3D/2019.09.11 Редуктор бутылкореза V0.9.f3d
V0.9 - Alfa /3D/STL/01-04 Бушинг-нужно 4шт.stl
V0.9 - Alfa /3D/STL/01-05 Распорка-нужно 4шт.stl
V0.9 - Alfa /3D/STL/02-02 Спейсер(1) средней шестерни.stl
V0.9 - Alfa /3D/STL/02-03 Спейсер(2) средней шестерни.stl
V0.9 - Alfa /3D/STL/03-01 Шестерня бобины.stl
V0.9 - Alfa /3D/STL/03-02 Тело бобины.stl
V0.9 - Alfa /3D/STL/03-03 Крышка бобины.stl
V0.9 - Alfa /3D/STL/03-04 Спейсер(1) бобины.stl
V0.9 - Alfa /3D/STL/03-05 Спейсер(2) бобины.stl
V0.9 - Alfa /3D/STL/04 шестерня для мотора.stl
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

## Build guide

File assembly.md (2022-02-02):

# Копус станка

Для сборки станка понадобится длинная шпилька с резьбой из строительного магазина диаметром 5мм. 
Её отрезками скрепляются две половинки станка, с установленными между ними шестернями.
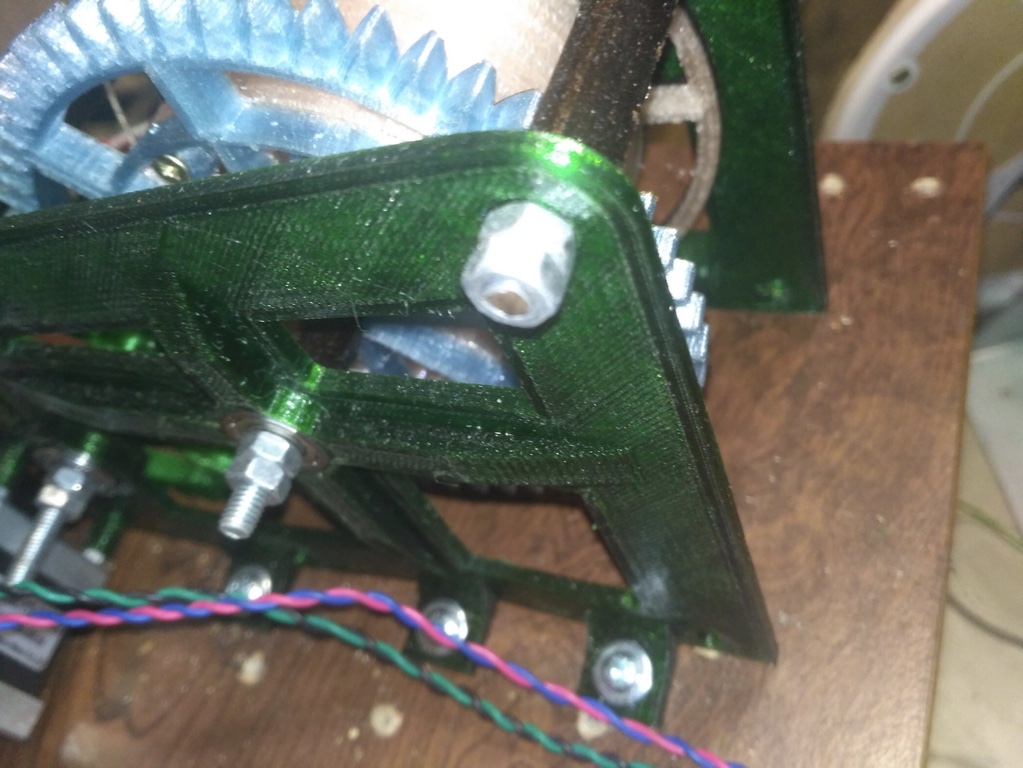
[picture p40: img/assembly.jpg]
assembly


Стенки станка распечатывается любым видом пластика.  
Шестерни из PET более подходят для работы нежели из ABS.  
Валы шестерен крепятся к корпусу через подшипники 625ZZ. 

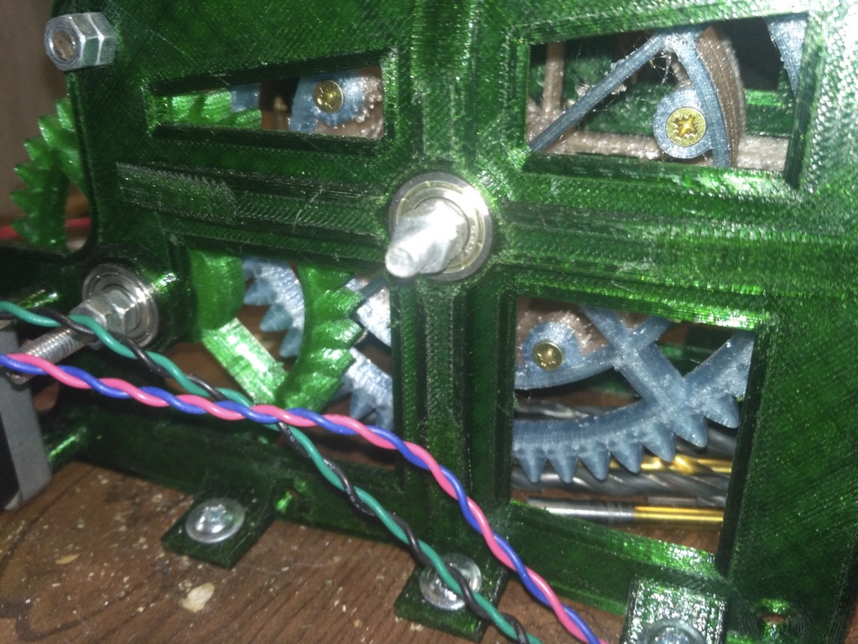
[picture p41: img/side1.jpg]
side1


За сто рублей в Китае можно купить 10 штук. 

- [ market.yandex? Q=625ZZ ](https://market.yandex.ru/catalog--zapchasti/54459/list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)
- [aliexpress Q=625ZZ](https://aliexpress.ru/wholesale?catId=0&initiative_id=SB_20220201201203&SearchText=625ZZ)

Если подшипников нет в наличии - можно временно распечатать из пластика втулки. 
Они включены в проект. Изготовленные из бутылочного PET - они работают достаточно хорошо и 
особенного износа (даже работая по резьбе шпилек) у них я не заметил.

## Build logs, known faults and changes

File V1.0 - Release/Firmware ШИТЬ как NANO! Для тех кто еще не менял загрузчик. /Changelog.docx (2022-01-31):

2020.01.04 V-1.4

Добавлено автоотключение нагревателя протяжки после 30 минут простоя.

Добавлено автоотключение нагревателя спайщика после 60 минут простоя.

Добавлена индикация неподключенного термодатчика нагревателя протяжки. (ошибка 1)

Добавлена индикация неподключенного термодатчика нагревателя спайщика. (ошибка 2)

Добавлена индикация перегрева термодатчика нагревателя протяжки выше 330 градусов. (ошибка 3)

Добавлена индикация перегрева термодатчика нагревателя спайщика выше 330 градусов. (ошибка 4)

Исправлена ошибка несохранения в памяти скорости вытяжки прутка.

Добавлено меню сброса настроек к заводским. Находится в самом верху. После активации дождаться перезагрузки, а затем включить и выключить питание.

2020.01.05 V-1.5

Написана реакция контроллера на отвал датчиков температуры протяжки. (ошибка 5)

Написана реакция контроллера на отвал датчиков температуры спайщика. (ошибка 6)

2020.09.18 V1.9

Переработана работа клавиатуры. Добавлено ускорение при удержании. Пофиксены ложные срабатывания кнопок.

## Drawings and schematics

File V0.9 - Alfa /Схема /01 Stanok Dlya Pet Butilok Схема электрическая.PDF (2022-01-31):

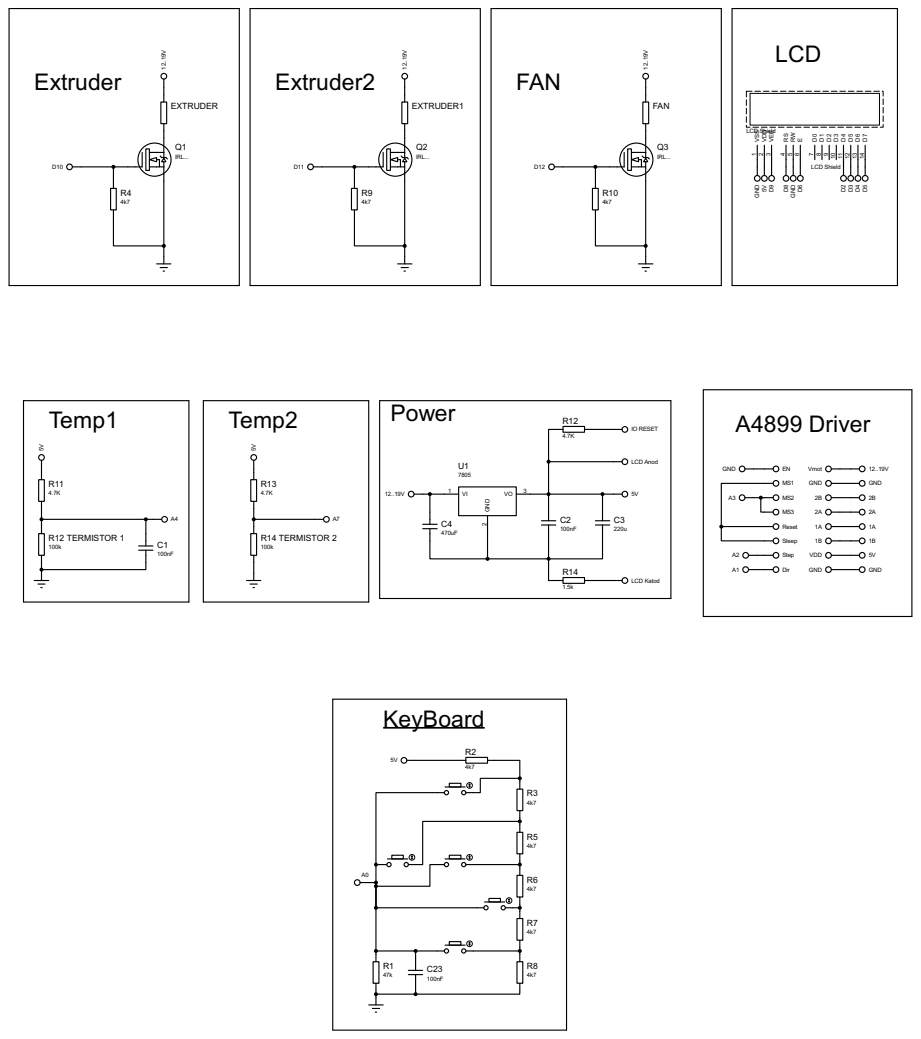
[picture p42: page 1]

ENMS1 MS2 MS3 Reset Sleep Step Dir

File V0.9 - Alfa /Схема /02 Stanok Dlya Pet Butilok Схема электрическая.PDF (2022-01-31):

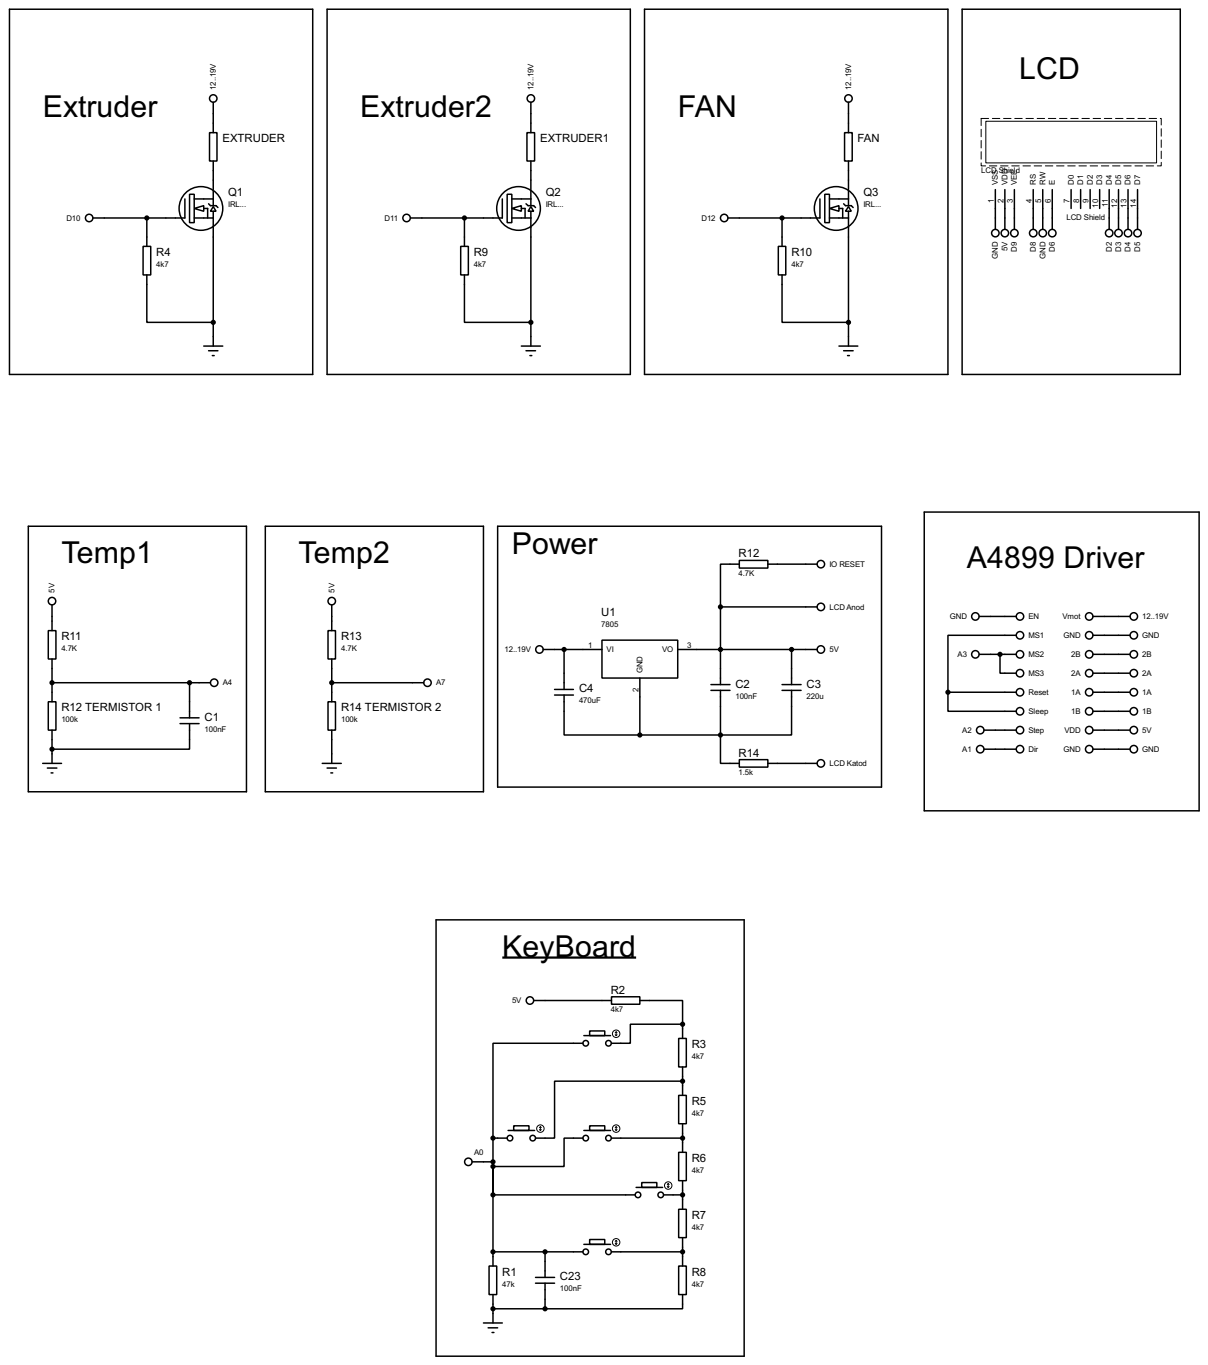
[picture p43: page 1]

ENMS1 MS2 MS3 Reset Sleep Step Dir

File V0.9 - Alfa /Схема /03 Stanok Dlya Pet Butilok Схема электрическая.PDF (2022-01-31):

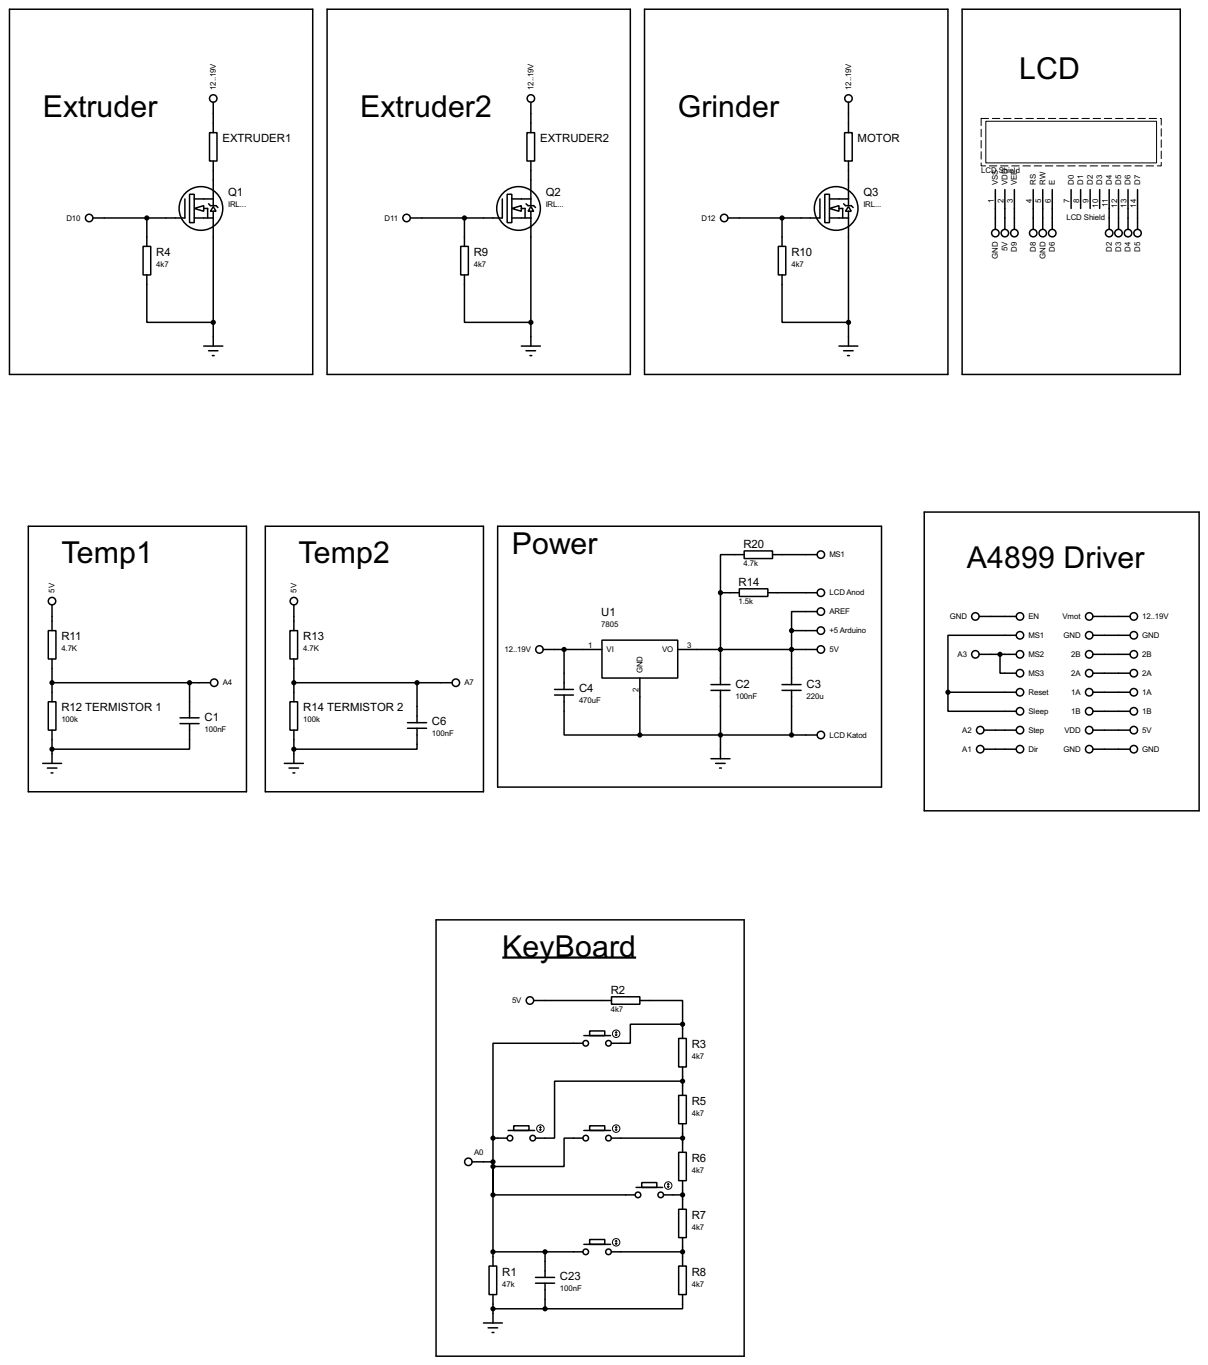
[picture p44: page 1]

ENMS1 MS2 MS3 Reset Sleep Step Dir

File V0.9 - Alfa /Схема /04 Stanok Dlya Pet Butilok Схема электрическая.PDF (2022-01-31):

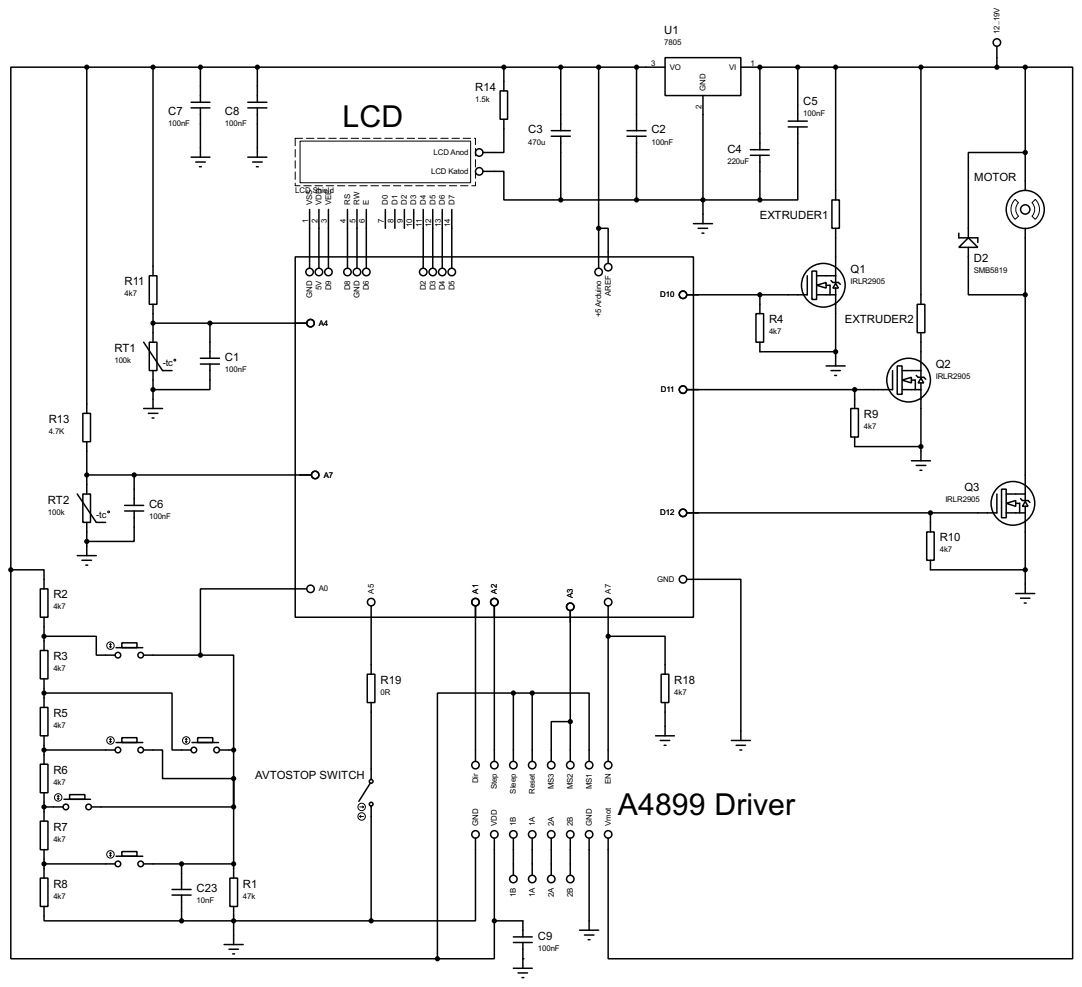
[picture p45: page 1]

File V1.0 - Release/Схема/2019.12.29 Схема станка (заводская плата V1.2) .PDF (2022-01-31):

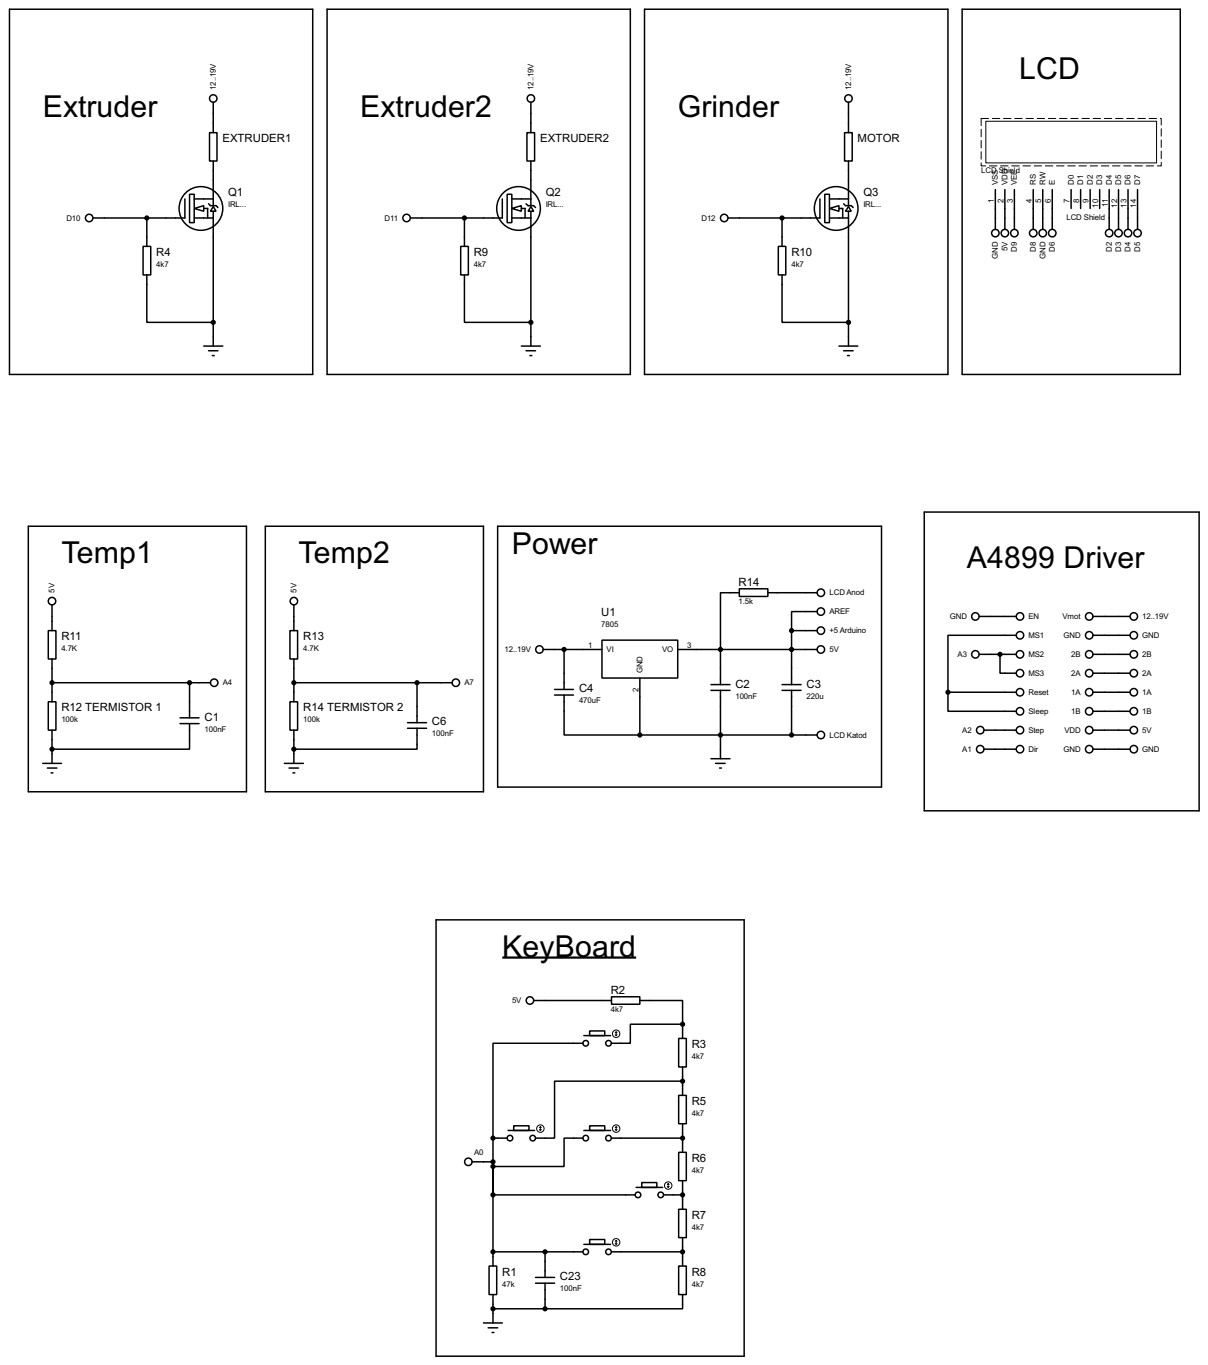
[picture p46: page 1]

ENMS1 MS2 MS3 Reset Sleep Step Dir

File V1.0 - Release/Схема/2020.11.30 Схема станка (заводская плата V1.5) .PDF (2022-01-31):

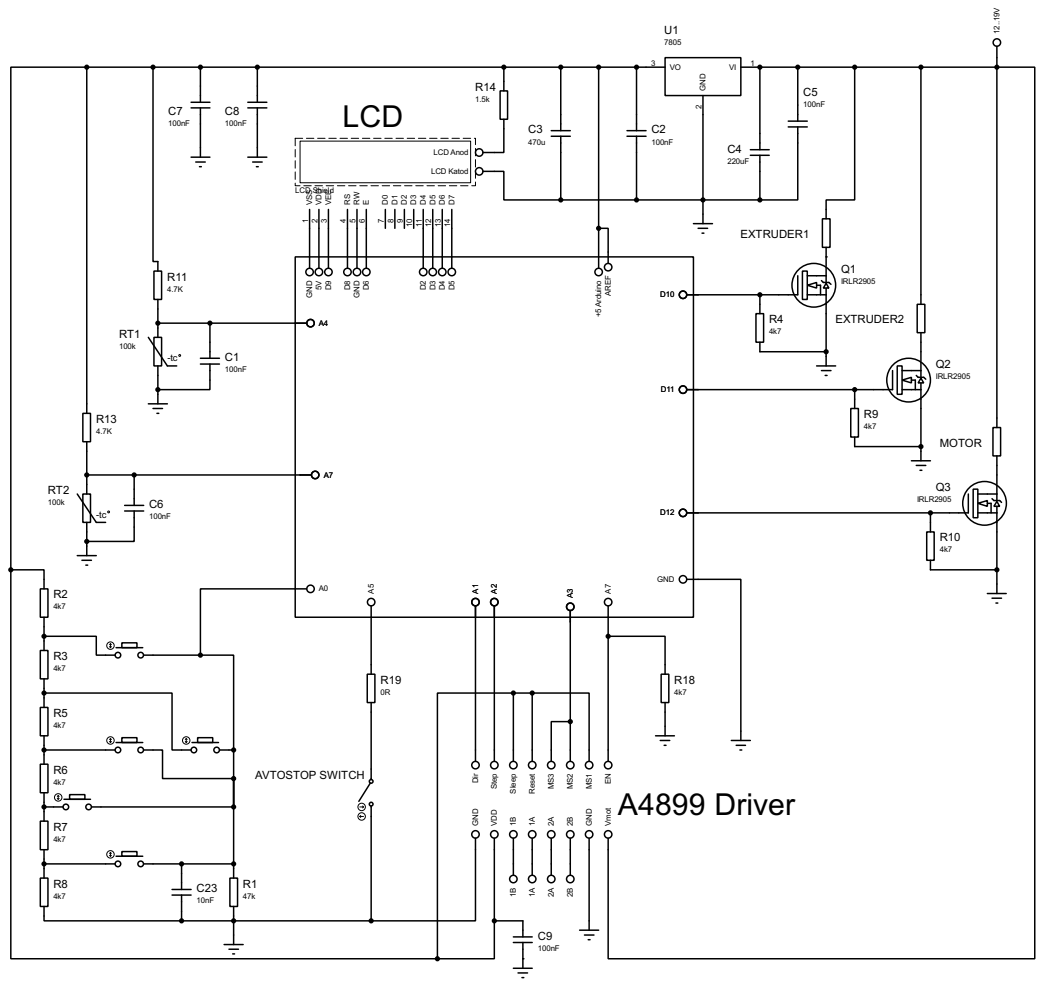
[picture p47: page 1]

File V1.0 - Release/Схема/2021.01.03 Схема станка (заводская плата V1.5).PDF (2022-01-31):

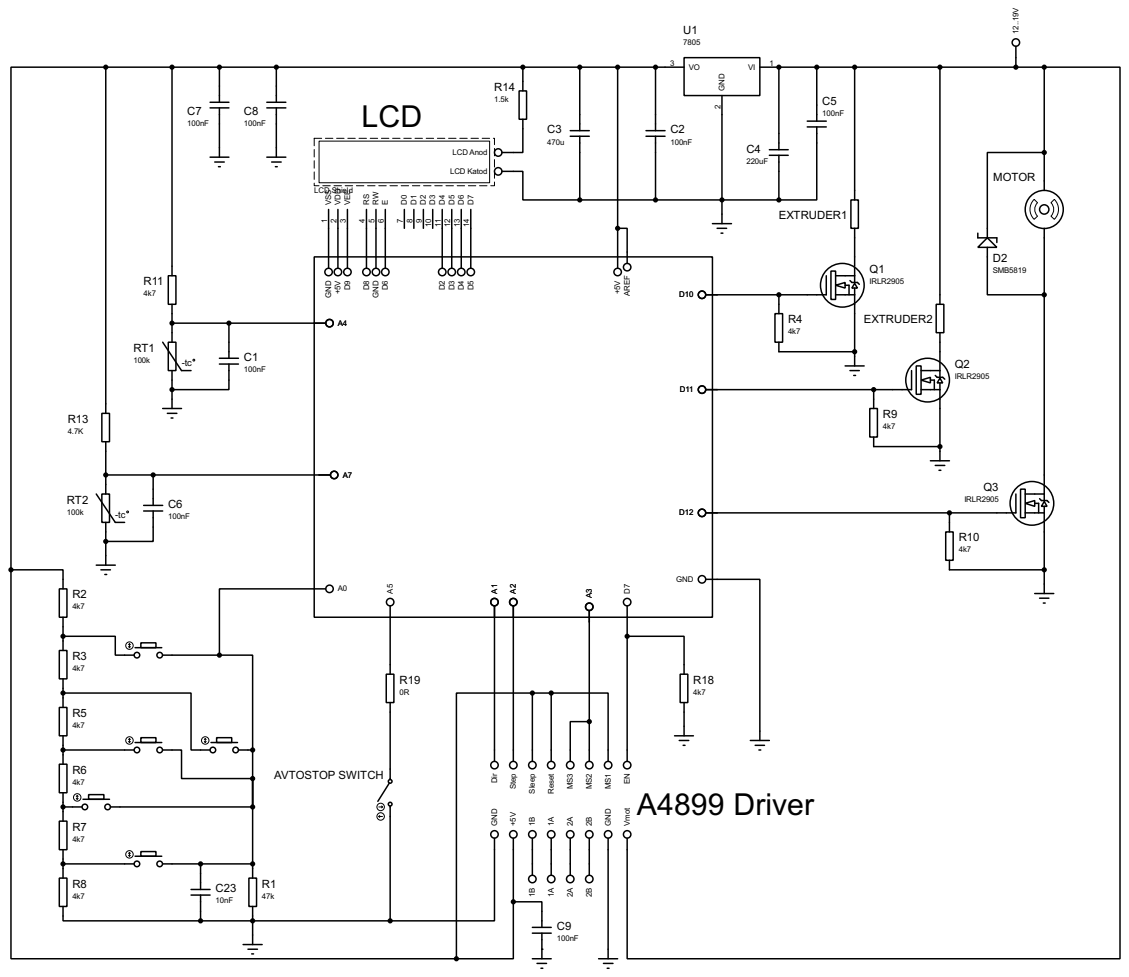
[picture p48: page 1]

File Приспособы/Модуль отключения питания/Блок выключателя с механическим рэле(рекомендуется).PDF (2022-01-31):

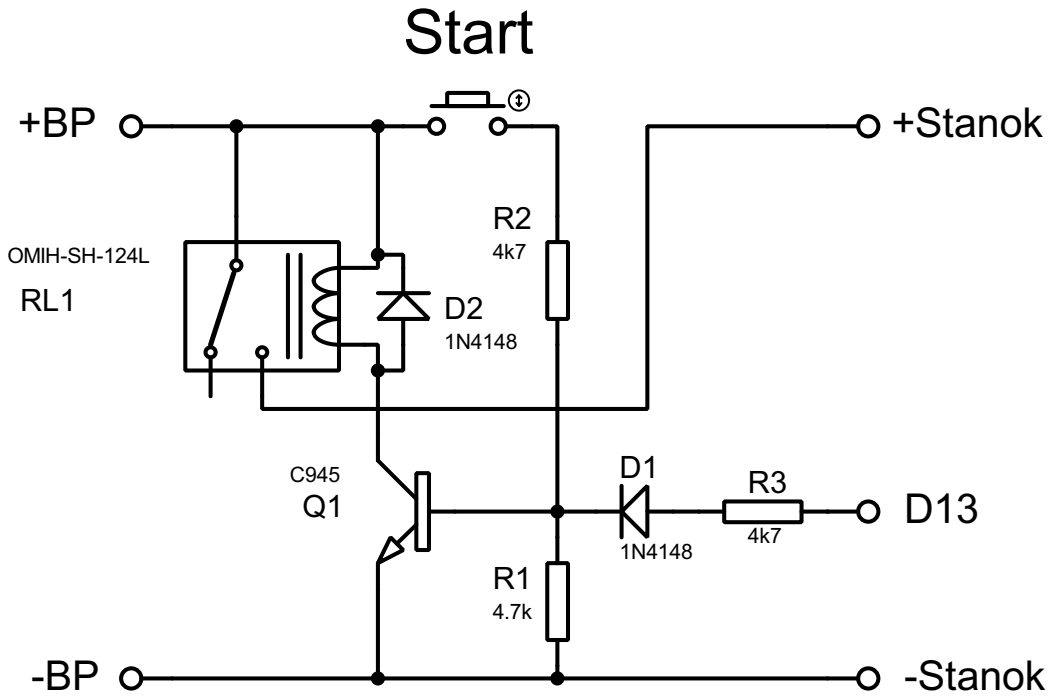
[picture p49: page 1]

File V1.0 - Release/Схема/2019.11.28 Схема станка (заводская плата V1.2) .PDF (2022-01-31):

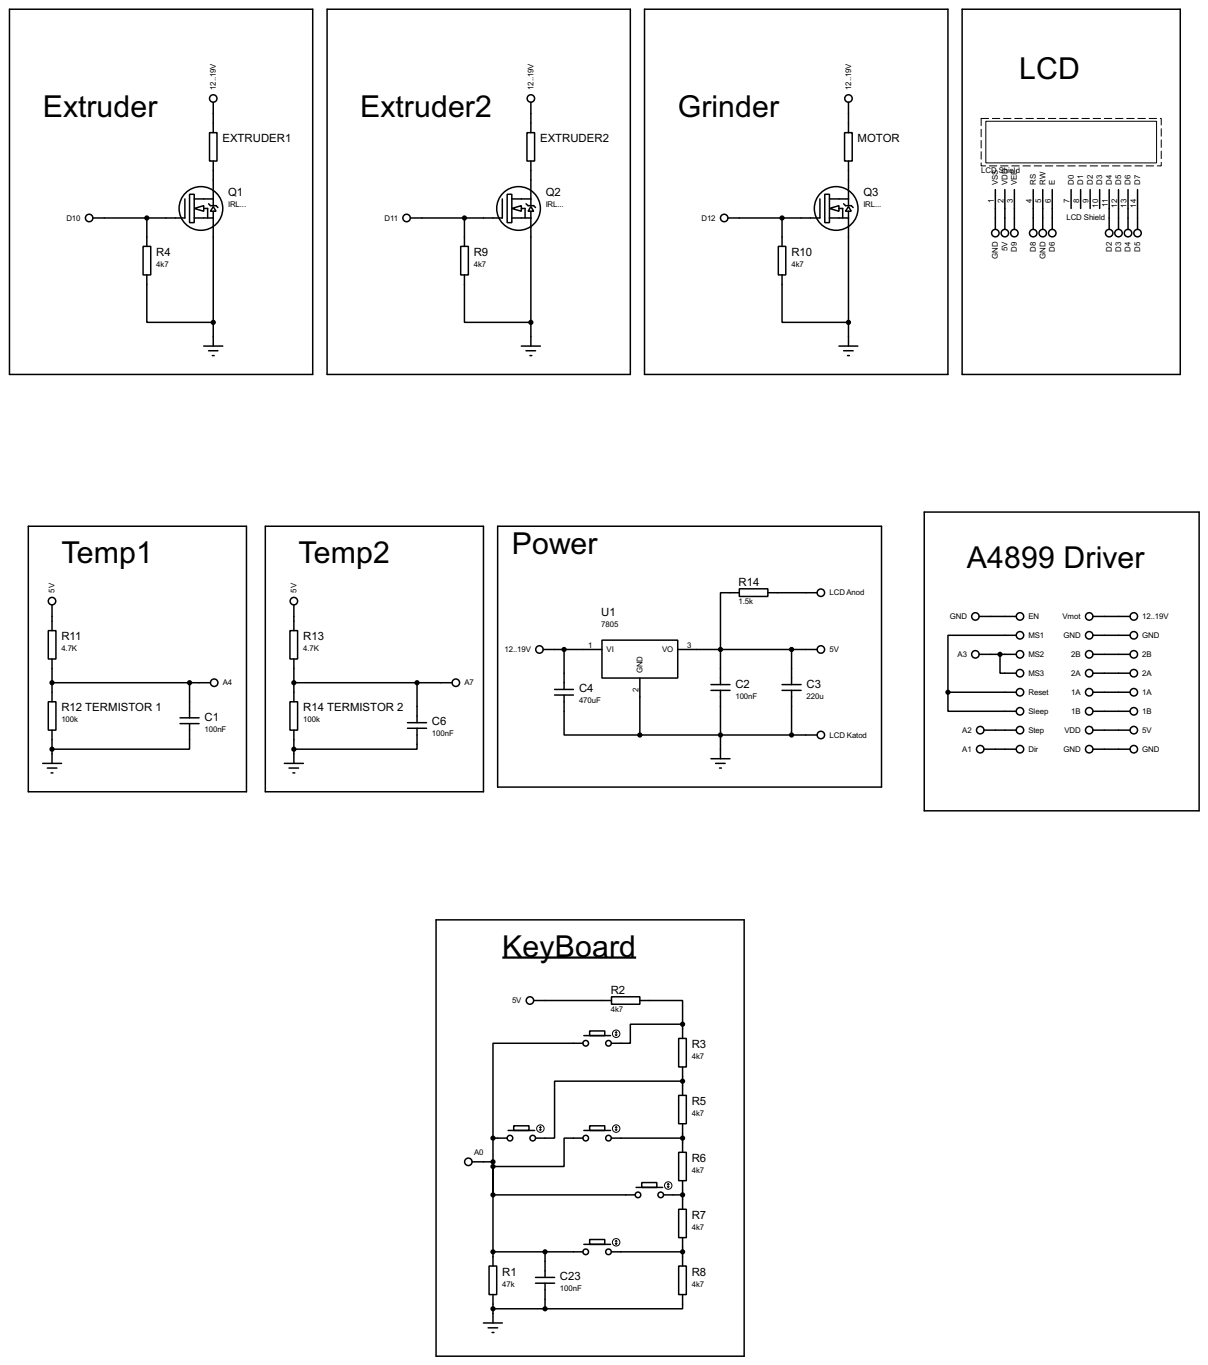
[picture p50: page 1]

ENMS1 MS2 MS3 Reset Sleep Step Dir
